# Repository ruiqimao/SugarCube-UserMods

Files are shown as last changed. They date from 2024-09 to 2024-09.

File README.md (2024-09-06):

# SugarCube User Mods

A collection of user-created modifications for [SugarCube](https://github.com/ruiqimao/SugarCube). To submit a mod, please create a folder in [Mods](Mods) named `username-modname` and update the index below.

## Index

| Name | Creator | Description | Link |
|:-|:-|:-|:-|
| Live Shaft / 2020 Backer | Burgo | Adds live shaft idlers and a 2020 X backer | [Link](Mods/Burgo-Live-Shaft-2020-Backer) |
| Button Corner | ruiqimao | Adds a stealthy button to a skirt corner | [Link](Mods/ruiqimao-Button-Corner) |
| Micron Spool Holder | ruiqimao | Mount for a Micron R1 removable spool holder | [Link](Mods/ruiqimao-Micron-Spool-Holder) |

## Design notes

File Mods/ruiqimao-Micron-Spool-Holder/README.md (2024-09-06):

# Micron Spool Holder

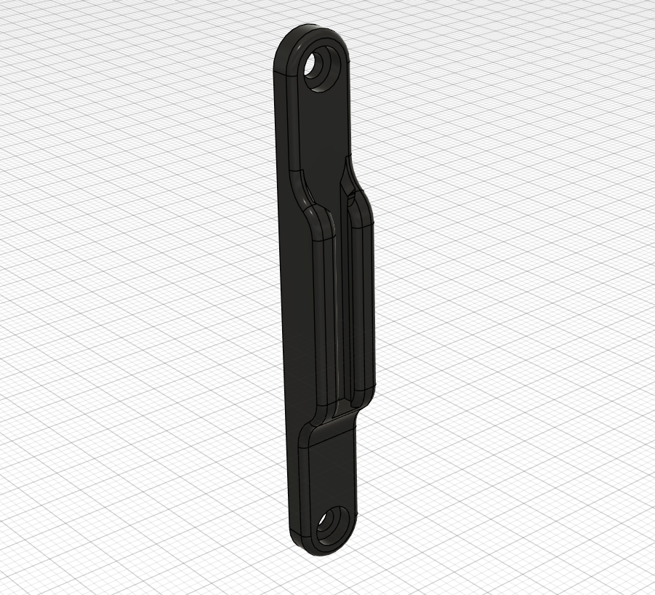
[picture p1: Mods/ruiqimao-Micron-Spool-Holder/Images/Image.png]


This is a mount for the removable spool holder from [Micron R1](https://github.com/PrintersForAnts/Micron). It mounts to the back panel of the printer, similar to the reverse Bowden holder.

| Part | Quantity |
|:-|:-:|
| M3x12 BHCS | 2 |
| 2mm ID x 4mm OD x 87mm PTFE tube | 1 |

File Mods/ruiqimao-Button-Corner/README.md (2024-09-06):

# Button Corner

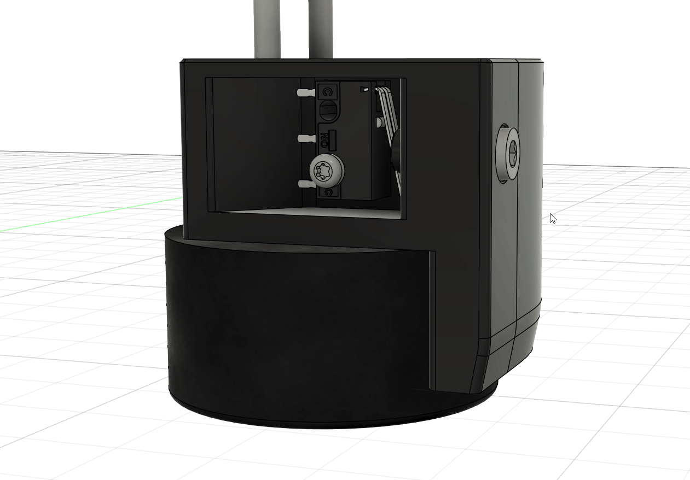
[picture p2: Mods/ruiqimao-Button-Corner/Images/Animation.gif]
Animation


This mods adds a stealthy integrated button into a skirt corner. In addition to the parts required for a regular skirt corner, this mod requires:

| Part | Quantity |
|:-|:-:|
| M3x10 SHCS | 1 |
| M2x10 self tapper | 1 |
| 3mm ID x 4mm OD x 7mm length PTFE tube | 1 |
| D2F-L microswitch | 1 |

## Klipper configuration

This sample configuration can be used to customize the behavior of single, double, triple, and long presses of the button.

```
[gcode_button action]
pin: # INSERT PIN.
press_gcode: _ACTION_PRESS
release_gcode: _ACTION_RELEASE

[gcode_macro ACTION_BUTTON]
variable_count: 0
variable_delay: 0.2
variable_long: 1.0
gcode:
    {% set long = params.LONG|default(0)|int %}
    {% if long == 1 %}
        # INSERT LONG PRESS GCODE.
    {% else %}
        {% if count == 1 %}
            # INSERT SINGLE PRESS GCODE.
        {% endif %}
        {% if count == 2 %}
            # INSERT DOUBLE PRESS GCODE.
        {% endif %}
        {% if count >= 3 %}
            # INSERT TRIPLE PRESS GCODE.
        {% endif %}
    {% endif %}

[gcode_macro _ACTION_PRESS]
gcode:
    {% set vars = printer["gcode_macro ACTION_BUTTON"] %}
    _ACTION_CANCEL_DELAY
    SET_GCODE_VARIABLE MACRO=ACTION_BUTTON VARIABLE=count VALUE={vars.count|int + 1}
    UPDATE_DELAYED_GCODE ID=_ACTION_LONG_EXECUTE DURATION={vars.long}

[gcode_macro _ACTION_RELEASE]
gcode:
    {% set vars = printer["gcode_macro ACTION_BUTTON"] %}
    _ACTION_CANCEL_DELAY
    UPDATE_DELAYED_GCODE ID=_ACTION_EXECUTE DURATION={vars.delay}

[gcode_macro _ACTION_RESET]
gcode:
    SET_GCODE_VARIABLE MACRO=ACTION_BUTTON VARIABLE=count VALUE=0

[gcode_macro _ACTION_CANCEL_DELAY]
gcode:
    UPDATE_DELAYED_GCODE ID=_ACTION_EXECUTE DURATION=0
    UPDATE_DELAYED_GCODE ID=_ACTION_LONG_EXECUTE DURATION=0

[delayed_gcode _ACTION_EXECUTE]
gcode:
    _ACTION_CANCEL_DELAY
    ACTION_BUTTON
    _ACTION_RESET

[delayed_gcode _ACTION_LONG_EXECUTE]
gcode:
    _ACTION_CANCEL_DELAY
    ACTION_BUTTON LONG=1
    _ACTION_RESET
```

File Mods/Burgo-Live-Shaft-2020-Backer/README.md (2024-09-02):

Adds a 2020 Extrusion with full access to the 120mm of the bed!

Removes all of the 20t idlers in SugarCube instead using 16t and 20t pulleys with F623 bearings making them have almost 1.5x better load bearing capability. To do this Shaft reducers are required such as https://www.tinkerforge.com/en/shop/shaft-reducer-5mm-3mm.html however a mix of 15.5mm and 16mm is required.
5mmODx1mm Wall Thickness Steel Tube cut into 4 15.5mm and 2 16mm is an alternative.

> [!IMPORTANT]  
> You will need to grind down 1 16t Pulley so it has .5mm of flange instead of 1.5mm (removing 1mm), the mod would change the length of all screws which would mean none work otherwise.

> [!IMPORTANT]  
> Retaining Compound is needed for bearings and the shaft reducers in this mod

> [!WARNING]  
> This mod is MEANT for Gates Pulleys, other pulleys may have different overall length.

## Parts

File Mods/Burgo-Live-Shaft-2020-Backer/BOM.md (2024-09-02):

[SendCutSend Cart](https://cart.sendcutsend.com/qsqcrl6fotax)

Additions:
| Part | Quantity | Link |
|:-|:-:|:-|
| F623 bearing | 12 | [Misumi](https://us.misumi-ec.com/vona2/detail/221000528976/) |
| 20 tooth GT2 pulley | 2 | [McMaster-Carr](https://www.mcmaster.com/3684N12/) |
| 16 tooth GT2 pulley | 2 | [McMaster-Carr](https://www.mcmaster.com/3684N11/) |
| 3x25mm Shoulder Bolt with 4mm Thread length | 2 | [Misumi](https://us.misumi-ec.com/vona2/detail/223304079707/?HissuCode=ZR1695-303H) |
| 3mm x 28.5mm pin | 2 | [Misumi](https://us.misumi-ec.com/vona2/detail/110100140710/) (cut to size) |
| 3mm x 37mm pin | 4 | [Misumi](https://us.misumi-ec.com/vona2/detail/110100140710/) (cut to size) |
| M5x8mm BHCS | 4 | [BoltDepot](https://boltdepot.com/Product-Details?product=22786) |
| M5x10mm BHCS | 4 | [BoltDepot](https://boltdepot.com/Product-Details?product=22785) |
| M3x45mm SHCS | 6 | [BoltDepot](https://boltdepot.com/Product-Details?product=22478) |
| M3x2mm Alu Spacer | 2 | [McMaster-Carr](https://www.mcmaster.com/94669A212/) |
| M3x22mm Alu Spacer | 2 | [McMaster-Carr](https://www.mcmaster.com/94669A319/) |
| 5mmODx1mm Wall Thickness Steel Tube x250mm | 1 | [Aliexpress](https://www.aliexpress.us/item/4001197346556.html) |
| 10mm Reamer | 1 | [Aliexpress](https://www.aliexpress.com/item/1005003095896937.html) |
| 3x5x.5 Shims | Buy 50 | [Aliexpress](https://www.aliexpress.com/item/1005004445368257.html) |
| 3x6x1 Shims | Buy 50 | [Aliexpress](https://www.aliexpress.com/item/1005004445368257.html) |

Removals:
| Part | Quantity | New Total |
|:-|:-:|:-|
| 3mm x 27mm pin | 2 | 10 |
| 5mm x 27mm pin | 6 | 3 |
| M3x25 BHCS | 2 | 4 |
| M3x25 SHCS | 2 | 0 |
| M3x8 BHCS | 8 | 0 |

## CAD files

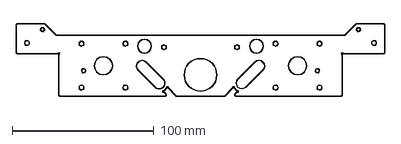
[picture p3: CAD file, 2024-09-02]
Mods/Burgo-Live-Shaft-2020-Backer/DXFs/Sugarcube Live Shaft Top Motor Mount x1.dxf
260.0 x 51.0 mm

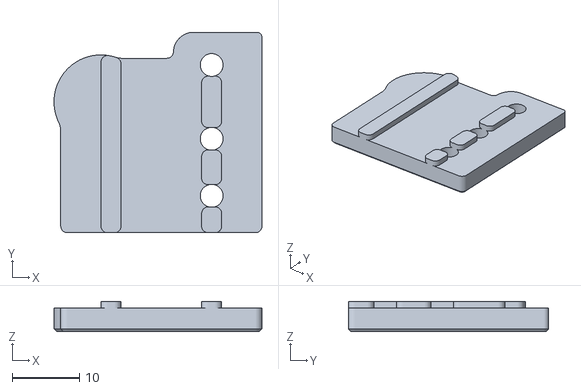
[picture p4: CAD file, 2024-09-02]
Mods/Burgo-Live-Shaft-2020-Backer/STLs/Left Front Idler Spacer x1.stl
31.0 x 29.9 x 4.50

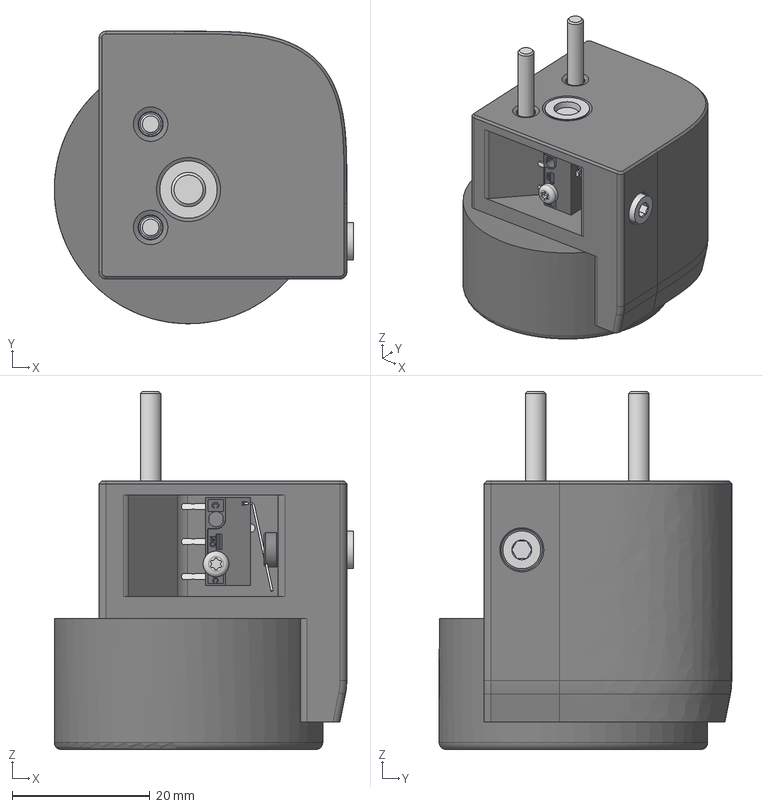
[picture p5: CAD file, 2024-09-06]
Mods/ruiqimao-Button-Corner/CAD/Button_Corner.step
43.5 x 42.5 x 52.0 mm
M3x30 SHCS x 2
94180A361_NO THREADS_Tapered Heat-Set Inserts for Plastic(Mirror)(Mir ror)
Rubber Foot v1(Mirror)(Mirror)
M5x30 BHCS v1(Mirror)(Mirror)
M3x10 SHCS
Switch Body
Lever
Contacts
Plunger
M2x10 STS
PTFE Tube
Stopper

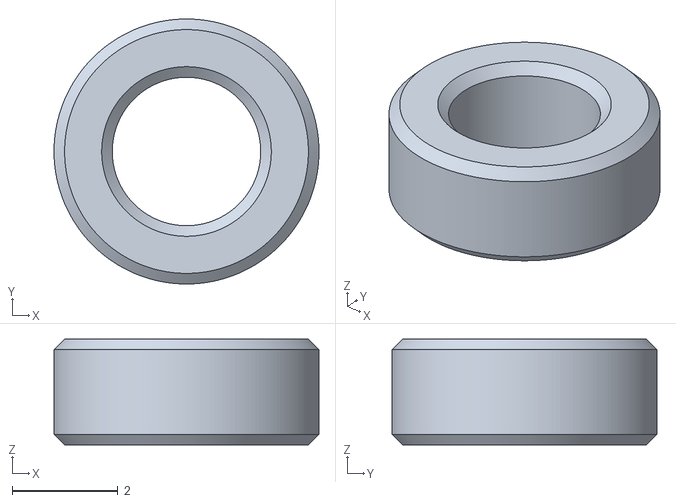
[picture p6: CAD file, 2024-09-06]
Mods/ruiqimao-Button-Corner/STLs/Stopper.stl
5.00 x 5.00 x 2.00

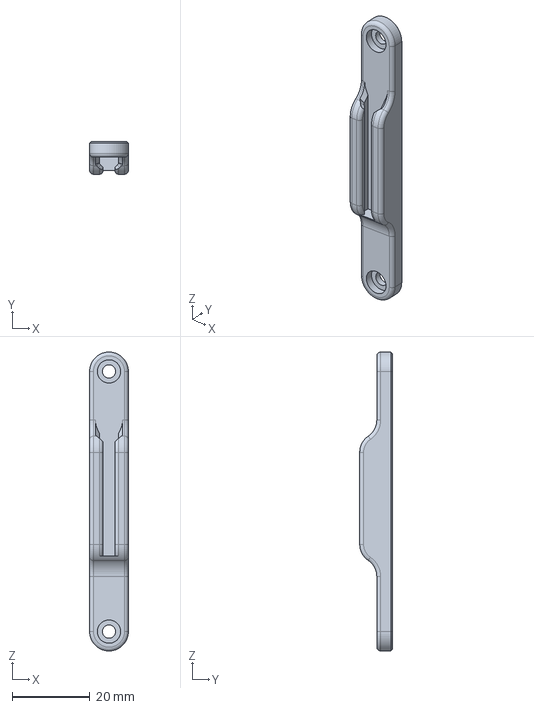
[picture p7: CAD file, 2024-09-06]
Mods/ruiqimao-Micron-Spool-Holder/CAD/Micron_Spool_Holder.step
10.0 x 8.40 x 77.0 mm

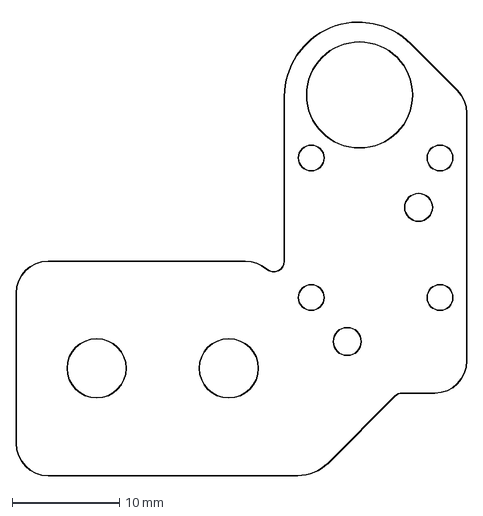
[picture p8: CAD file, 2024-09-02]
Mods/Burgo-Live-Shaft-2020-Backer/DXFs/Sugarcube 2020 Bottom XY Joint x2.dxf
42.0 x 42.8 mm

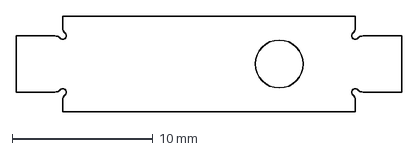
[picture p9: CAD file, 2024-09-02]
Mods/Burgo-Live-Shaft-2020-Backer/DXFs/Sugarcube Motor Tensioner Plate x2.dxf
27.4 x 6.76 mm

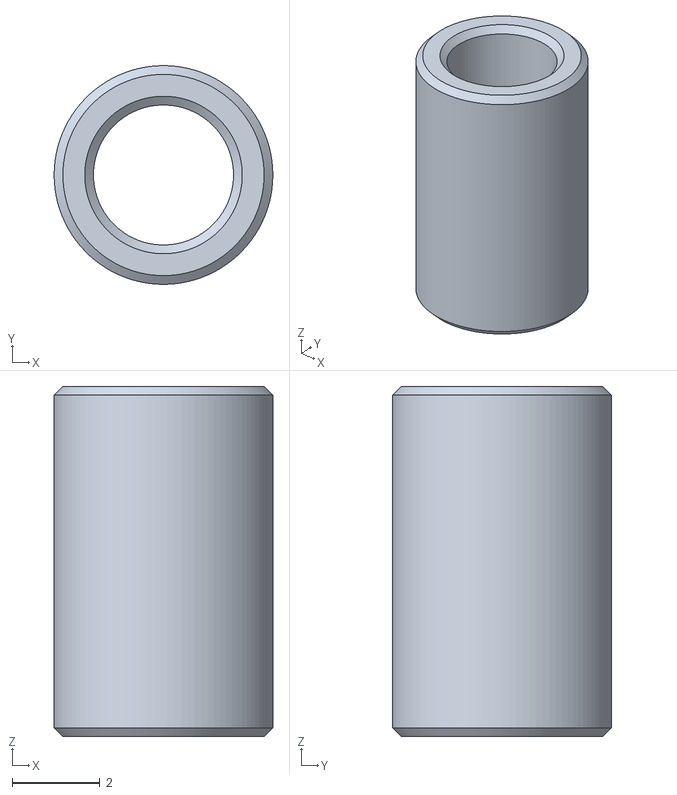
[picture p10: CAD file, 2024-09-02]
Mods/Burgo-Live-Shaft-2020-Backer/STLs/8mm Spacer x1.stl
5.00 x 5.00 x 8.00

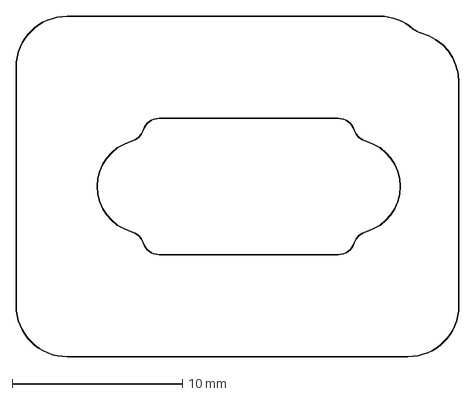
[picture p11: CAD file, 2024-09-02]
Mods/Burgo-Live-Shaft-2020-Backer/DXFs/Sugarcube 2020 Spacer XY Joint x2.dxf
26.0 x 20.0 mm

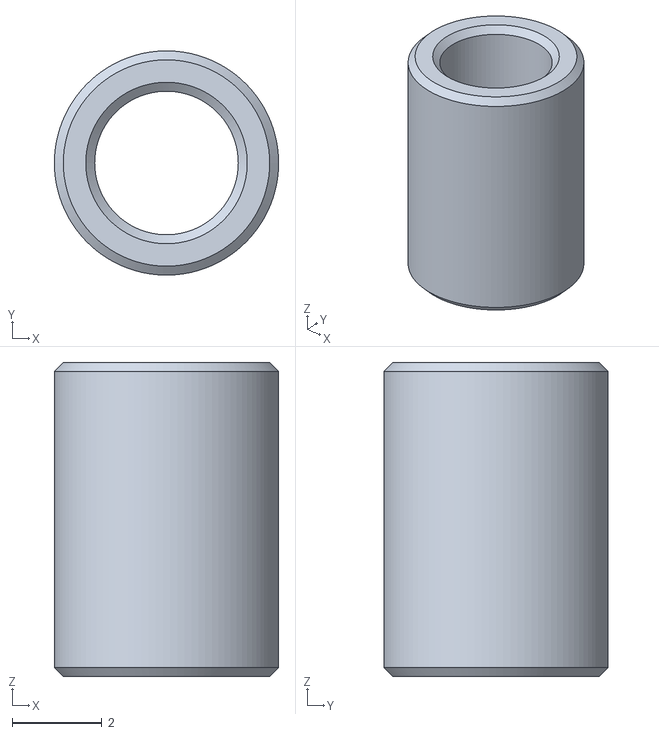
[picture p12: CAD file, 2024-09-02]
Mods/Burgo-Live-Shaft-2020-Backer/STLs/7mm Spacer x1.stl
5.00 x 5.00 x 7.00

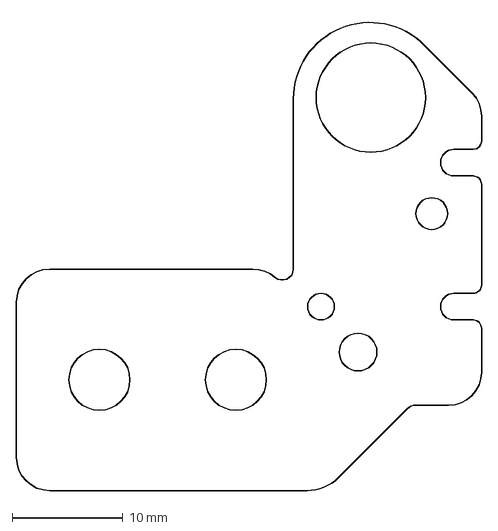
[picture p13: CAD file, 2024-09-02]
Mods/Burgo-Live-Shaft-2020-Backer/DXFs/Sugarcube Top XY Joint x2.dxf
42.0 x 42.8 mm

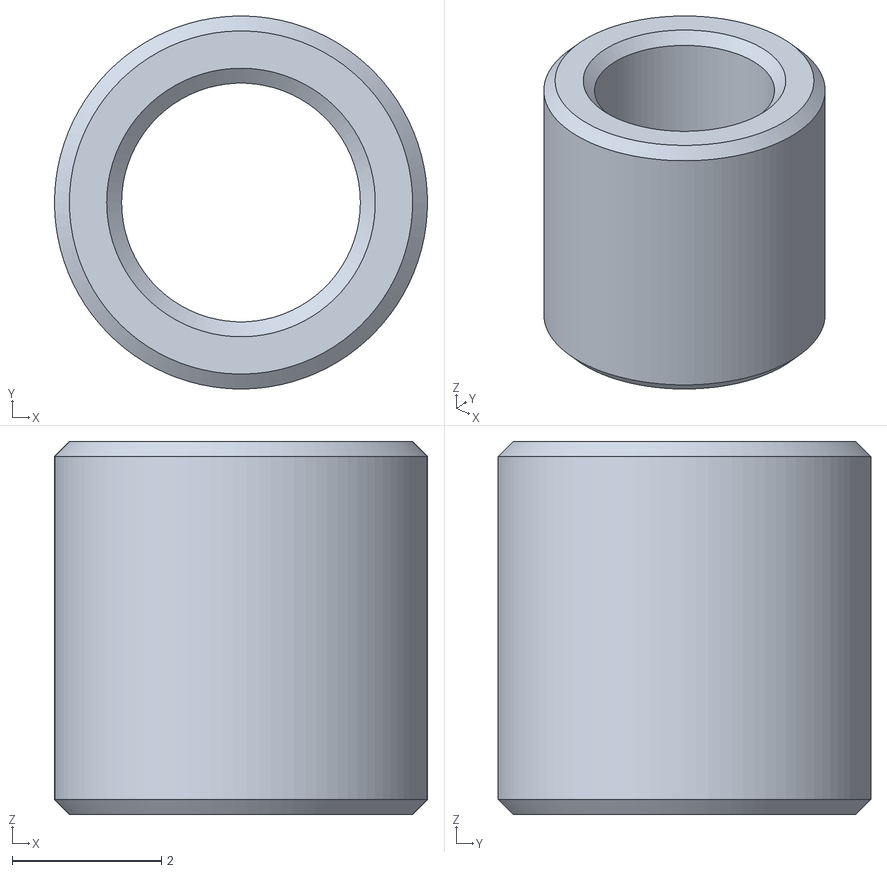
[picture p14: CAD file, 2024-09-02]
Mods/Burgo-Live-Shaft-2020-Backer/STLs/5mm Spacer x2.stl
5.00 x 5.00 x 5.00

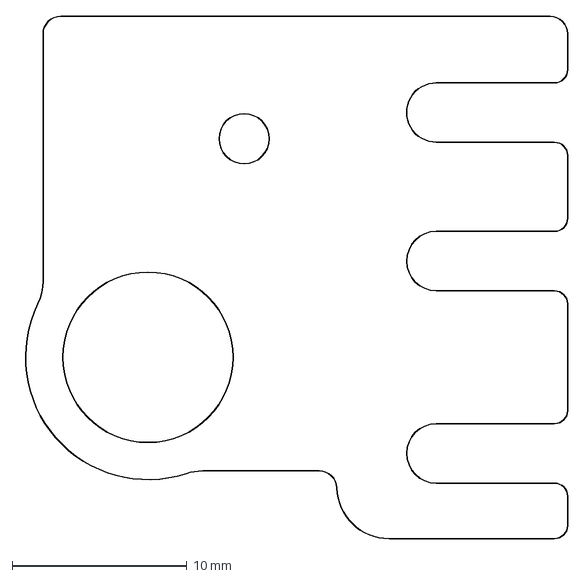
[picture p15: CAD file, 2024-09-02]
Mods/Burgo-Live-Shaft-2020-Backer/DXFs/Sugarcube Front Idler Panels x4.dxf
31.5 x 29.9 mm

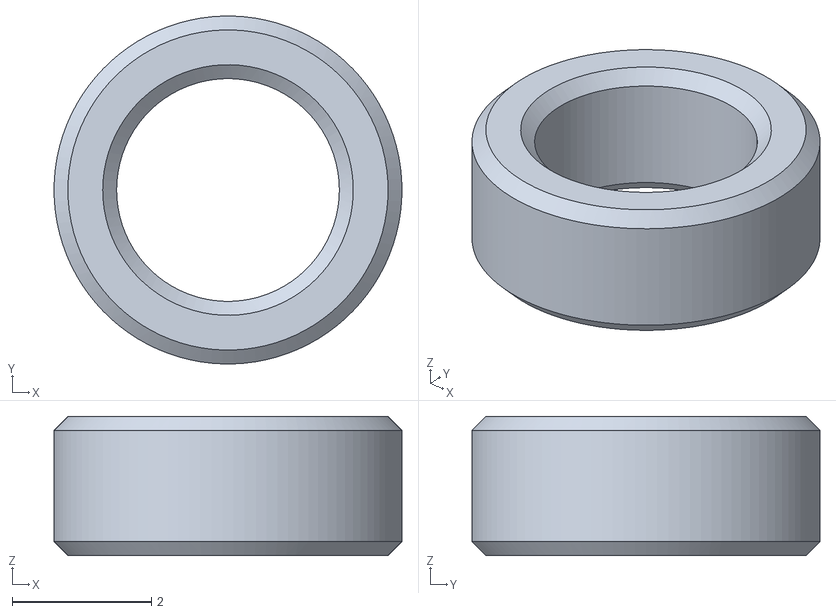
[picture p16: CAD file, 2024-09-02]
Mods/Burgo-Live-Shaft-2020-Backer/STLs/2mm Spacer x1.stl
5.00 x 5.00 x 2.00

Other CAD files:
Mods/ruiqimao-Micron-Spool-Holder/STLs/Mount.stl
Mods/Burgo-Live-Shaft-2020-Backer/STLs/Right Front Idler Spacer x1.stl
Mods/Burgo-Live-Shaft-2020-Backer/DXFs/Sugarcube Live Shaft Bottom Motor Mount x1.dxf
Mods/Burgo-Live-Shaft-2020-Backer/STLs/Idlers Internal Spacer x2.stl
Mods/Burgo-Live-Shaft-2020-Backer/STLs/10mm Spacer x2.stl
Mods/Burgo-Live-Shaft-2020-Backer/STLs/6mm Spacer x1.stl
Mods/ruiqimao-Button-Corner/STLs/Button_Corner.stl
Mods/ruiqimao-Micron-Spool-Holder/STLs/Micron_Spool_Holder.stl

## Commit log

2024-09-02 Add First mods
    [10mm Spacer x2.stl, 2mm Spacer x1.stl, 5mm Spacer x2.stl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]
2024-09-02 Fix BOM
2024-09-06 Add files for Button-Corner mod
    [Button_Corner.step, Button_Corner.stl, Stopper.stl]
2024-09-06 Create Button-Corner README.md
2024-09-06 Add animation for Button-Corner
2024-09-06 Add files for Micron spool holder
    [Micron_Spool_Holder.step, Micron_Spool_Holder.stl, Mount.stl]
